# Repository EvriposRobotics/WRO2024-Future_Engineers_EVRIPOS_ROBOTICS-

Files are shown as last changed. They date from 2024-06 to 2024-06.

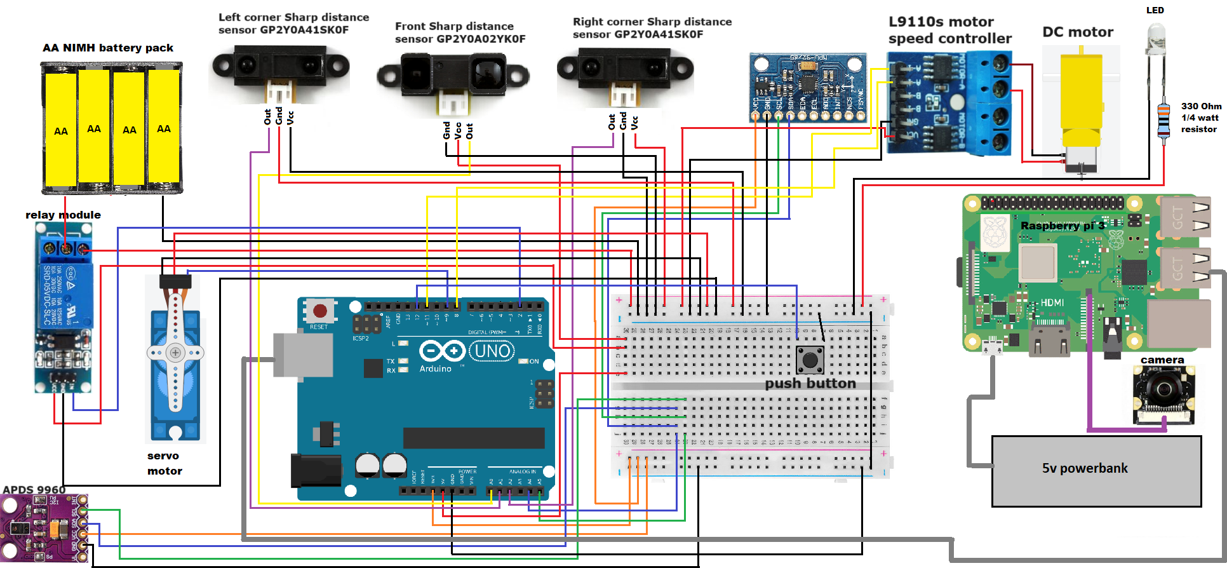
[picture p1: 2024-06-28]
schemes/electronics_wiring.png

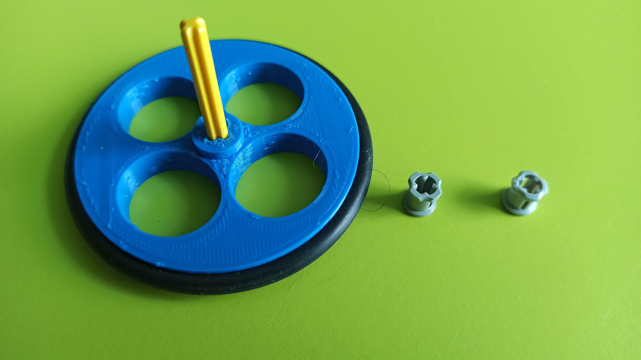
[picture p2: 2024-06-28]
models/front wheel semi-assembled.jpg

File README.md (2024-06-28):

**Evripos Robotics General Project Description (Future Engineers WRO 2023)**

The robot consists of a chassis that is entirely designed by Evripos Robotics team, excluding the rear axle mounted differential for which we used the design by "Luciano Ricardo de Faria", taken from the thingiverse.com repository :
 ([https://www.thingiverse.com/thing:3270976]).
 
The chassis was 3D printed using the "Creality Ender 3 v2" 3d printer with the use of PLA type plastic. Some sanding may need after 3D printing on some parts in order to have a perfect fit with others parts or to rotate freely depending on the case.

Not printed parts are:
- Τhe wheels axles, which are LEGO axles. On the front wheels, 2 LEGO axles with a length of 39mm have been used using a clamp (LEGO bush) on each wheel. For the    rear wheels we used 2 LEGO axles of 72mm length. A small amount of silicone-teflon type lubricating grease has been placed at each friction-contact point of the axles      with other components.
- One rubber O-ring on each wheel, outer diameter 68mm and thickness 4mm. It is critical that the o-rings are of a good quality in order to have a good grip with the    track.
   
**Robot movement**

For the drive of the robot, a "tt dc gear motor" type motor was used operating at 3-6V voltage with maximum rotation speed of 130 rpm. The motor is powered by a battery pack of 4 AA NiMH batteries connected in series.

Speed control of the robot is performed by an L9110s dc motor controller which receives signal through the digital ports 8 & 11 of the Arduino. Port 11 provides a PWM type signal for speed control. For better control of the surrounding environment through the robot's sensors, the motor speed has not been set to the motor’s maximum speed, as the PWM high-low pulse ratio does not exceed 50% (50% PWM).

The steering control is done by a micro servo type motor (MG90s) with metal gears. The Arduino controls the rotation of the servomotor via digital port 9. The servomotor rotates at most of 50⁰ left or right relative to the straight line of movement resulting to the turn of the front wheels to the relevant angle/direction.

**Robot start**

To be able to start the robot for the challenges of the competition we connected a push button switch which gives a signal to the digital port 12 of the Arduino.

**Sensors**

Three (3) distance sensors, a color sensor, an accelerometer-gyroscope(IMU) and a wide camera are used for the needs of the robot's navigation inside the track:

- The front distance sensor: "Sharp GP2Y0A02YK0F" type infrared distance sensor with 4.5-5.5V power supply tolerance and 20-150cm distance detection range.
- The left and right corner distance sensors: "Sharp GP2Y0A41SK0F" type infrared distance sensors with 4.5-5.5V power supply tolerance and 4-30cm distance detection range.
- The color sensor: "APDS9960" type sensor with voltage supply of 3.3V which communicates with the Arduino using the I2C protocol. The sensor is powered from the Arduino Uno 3.3v power supply.
- Accelerometer-gyroscope sensor: “MPU6500” IMU type sensor with 3V-5V operating voltage which communicates with the Arduino using the I2C protocol. The sensor is powered from the Arduino Uno 3.3v power supply.
- Camera: “Waveshare Raspberry Pi camera module fisheye lens(m)” camera type sensor with 5MP resolution and 200° viewing angle.

(The two sensors that communicate using the I2C protocol are connected to the Arduino through the analog input ports A4 & A5 which have the role of the SDA and SCL ports of the protocol respectively).

**In details**

The front distance sensor (GP2Y0A02YK0F) is used to detect the walls of the track ahead, while the corner ones (GP2Y0A41SK0F) are used to detect if the vehicle approaches laterally to a wall or an obstacle.

When the robot gets close to a wall then the Arduino compares the 2 inputs it receives from the 2 corner distance sensors (left/right), compares the two distance inputs and then turns towards the direction of the sensor providing the higher distance (left/right).

Through the built-in motion processor (DMP-Digital Motion Processor) contained in the “MPU6500” sensor, which combines data from the accelerometer and the gyroscope, we continuously identify the orientation of the robot (in degrees) versus its initial position on the track. The sensor orientation error is less than 1⁰. When initializing the vehicle, the sensor initilization process sets the orientation to 0⁰. When the vehicle turns left the degrees increase up to 179.9⁰. When the robot turns right the degrees are reduced up to -179.9°. Out vehicle makes use o an algorithm which constantly corrects the path of the robot according to the continuously calculated desired path. 

The color sensor “APDS9960” detects the blue and orange lines of the track in order to accurately measure the number of turns the robot has performed but also to detect the direction to which the robot should turn to. If, for example, the robot meets the blue line first, then it understands that it should follow a counterclockwise trajectory on the track and thus must turn left on every at each subsequent corner.

The detection of the green & red pillars on the track is done through the raspberry pi model b+ which receives images through a 200⁰ fisheye camera with 5MP. At first the image is cropped, discarding the upper part of it as this is not needed for the obstacle detection and could create deviations if it detects off-track objects (keep only the useful track related image). In like manner, the left and right edges of the image is cropped reducing by a small degree the viewing angle of 200o that is not needed in our case, because the fisheye lens makes a black area nearly the edges of the received image.The raspberry pi processes the images by first cropping part of the field of view and then applying (via the opencv computer vision library) an algorithm that recognizes the red and green signals (obstacles) on the track. We apply a thershold above which a red or a green pillar is detected. Without the threshold the algorithm makes faulty detections of red or color objects. The we apply an algorithm that keeps only the largest colored object it detects. This object is that we must pass from left or right side accordingly to its color. The size of the object is calculated from its detected height.The walls of the track, which are black in color, are also detected for the robot in order to avoid them. The color system used to identify colors is HSV (Hue-Saturation-Value).

Finally, these data are processed appropriately and through the serial port (USB cable) connecting the raspberry pi to the Arduino, the data are sent in the form of string messages to the Arduino. The Arduino decodes these messages and then turns accordingly to avoid obstacles, taking also into account the inputs from the other sensors it manages. One message for example is “ns” which means no obstacle is detected ahead and another message is “l12s” which means turn the wheels to the left by 12⁰. So "l" means left steering, "r" means right steering, "n" means no steering and "s" is the stop character that arduino recognizes in order to decode the received characters string.

When there are no obstacles, the Arduino moves considering only the data from the other sensors (except the camera). 

**Light source & color detection**

We use a "cool white" color Light Emmitting Diode (LED), mounted at the bottom of the robot, next to the APDS9960 sensor. The purpose of this LED is to provide a strong light for the color sensor to make precise measurements of the track bottom colors. The led is connected to the power source using a 330 Ohm 1/4 Watt resistor in series as a protection. When the white color intensity falls bellow a level it means that the vehicle passing over a colored line. Then we check the dominant color. The color model of this sensor is RGB (Red-Green-Blue). So if the vehicle passing over a blue line the dominant color is blue and if passing over an orange line the dominant color is red.

**Electric power sources**

Two power sources are used:
1. A battery pack of 4 AA NiMH batteries in series (capacity 2450mAh) producing a total output voltage of 4.8V and is used for:
- the dc motor controller which powers the robot dc motor 
- the servo motor that helps the robot turn right or left
- the front infrared distance sensor
- the two (2) corner infrared distance sensors
- the white led
  
For more efficient energy consumption management of the electronic components powered by the above battery array, a relay board is used. This relay receives a logic level (5V) activation signal from the digital output port 2 of the Arduino Uno as soon as it starts, thus powering all connected devices to the battery pack. When the robot completes the activity on the track, the Arduino Uno is turning off by the user disconnecting its power cable, so that the relay stops powering these devices.

(**Caution:** Alkaline batteries should not be used for the array as the total voltage they produce (6V) is greater than the maximum allowable operating voltage of some electrical elements powered by the battery array).

2. A Χiaomi Powerbank (Mi powerbank 3 – 22.5W) with a total capacity of 10000mAh which exclusively powers the raspberry pi with an operating voltage of 5V via a USB micro B type cable. 

Notes about the power supply:
- The camera connected to the raspberry pi is powered through the CSI type cable connected to the corresponding port of the raspberry pi.
-	The Arduino is powered through the raspberry pi's USB port via a Male-A to Male-B USB cable.
-	The MPU6500 and APDS9960 sensors are powered by the 3.3V output of the Arduino Uno.

**SBC and SCM** 

The Single Board Computer used in our setup is the Raspberry Pi 3 model B+. The SBC in our case collects and processes the data (images) from the wide angle camera, at a rate of about 20-25 frames per second. Through this setup our robot is able to detect whether it has a red or a green pillar ahead or a black wall, deciding this way the angle the wheels must turn to avoid them the right way. The Raspberry Pi runs the official Raspberry Pi OS installed on a 32GB microsd card.

The Single Board Microcontroller used is the Arduino Uno rev2. The SBM receives data from various sensors and from the SBC via a serial (USB) cable. The SBM makes the final decisions for the robots movement (when to start, when to stop and when to turn) as it gives priority to the appropriate sensor according to the circumstances.

**Programming languages**

The Arduino Uno rev2  SBM used in our robot was programmed using the Arduino IDE 1.8.19 integrated programming environment with C++ language. The libraries used for Arduino are:
-	I2Cdev.h
-	MPU6050_6Axis_MotionApps20.h
-	Wire.h
-	Servo.h
-	Adafruit_APDS9960.h

Raspberry pi 3 SBC programming was done through Thonny integrated programming environment over Raspberry OS operating system. The programming language used was Python version 3.9.2, using extensively the opencv computer vision library. Other Python libraries used:
-	numpy
-	cv2 (opencv)
-	time
-	serial

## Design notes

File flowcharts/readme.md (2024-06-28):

**This folder contains the flowcharts that out algorithm follows for the WRO 2023 Future Engineer challenges:**
- The open challenge algorithm flowchart
- The obstacle challenge algorithm flowchart

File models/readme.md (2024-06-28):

**3D model of our vehicle**

For the 3D model of the robotic vehicle our team designed we provide a Tinkercad link:
https://www.tinkercad.com/things/f08WOoFHfk0?sharecode=AVScY2sZLryFHhnb4G2e9Pp45QpsDUL6hJvRQdBMmLM

We also extracted all the parts from entire model to .stl files and created a folder which contains these files that need to be 3d printed.

All the 3d design has been made using the online 3D modelling tool www.tinkercad.com.

Parts shown in black color represent the various electronic and electric devices used for the robot, so they are not need to be printed. Also the lego axles and bushes used for the wheels mounting are also shown in black color and they are not need to be printed. In green are the rubber o-rings which play the role of tires for our vehicle. These o-rings must be of 68mm outer diameter and and 4mm thickness. We chose them to be so thin so that our vehicle would have flexibility and could be easily driven with a small dc motor. 

Everything else shown in red color should be 3D printed. Parts fixation has been made using mostly m3 and some m2 bolts. The m2 bolts are used only for the parts that are mounted the upper plastic surface like the camera,the SBC and the SBM fixation, the prototype board etc. These board have small holes and m3 bolts cannot fin. Some parts do not need bolts to fit together as they designed for press fitting (for example, the wheels with the lego axles).

We include two photos showing the assembly of the front wheels. We use a lego technic yellow axle of 5L length and two grey lego technic bush bushings for each wheel. Lego bushings are used to secure the wheel on the 3d printed wheel hub.

We used the Ultimaker Cure 5.1.0 tool as a slicer. We used a Creality Ender 3 V2 3d printer to 3d print the parts. PLA plastic seems to be sturdy enough for the needs of the WRO Future Engineer contest and we have no accidents of broken parts so far.

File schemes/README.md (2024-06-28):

**Electronic/electric components wiring diagram**
The color of the cable indicates the type of function/connection it performs:

**Caution!!!
For the electronic components of the vehicle to work properly, the ground of the nimh battery pack (4x AA) must be connected to one of the ground points (marked as GND) on the arduino board.**

For easier management and connection of the power supply lines of the electronic components we have created a prototype board on which we have soldered a line for the 5v power supplies (from the nimh batteries) and a line for the grounding. Also on the same board we have placed a switch which serves to start the robot. The one pin of the button is connected to the ground and the other to the digital port 12 of arduino, used as a input for this case. The same thing can be done using a breadboard.

We included a 5v relay board to the output of which we have connected the 5v power supply from the battery. The relay is normally open and when it is given a high signal command from digital output 2 of the arduino then the circuit is closed and the electronic components that require 5v voltage are powered. In this way we save significant amounts of energy from the nimh battery pack and our vehicle gets much more autonomy.
The only devices powered by 3.3v are the mpu6050 gyroscope and the apds-9960 color sensor.

 - Wires in gray color: the two USB cables that connect a)Arduino Uno with Raspberry Pi 3 (usb type B cable) and b)Raspberry Pi 3 with the powerbank (usb micro B cable)
 - Wires in purple color: the special caCSI type cable than connects Raspberry Pi 3 to the Raspberry Pi  camera module
 - Wires in red color: the power lines at 5v.
 - Wires in orange color: the power lines at 3.3v
 - Wires in black color: the ground lines
 - Wires in the other colors: various signal input-output cables connecting on Arduino Uno

The "datasheets" subfolder inludes the datasheets of the Sharp distance sensors. The datasheets are useful because the output voltage of these sensor do not have a linear response accordingly to the calculated distance.

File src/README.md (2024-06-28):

**Source code files**

The folder named "arduino_code" contains two files:
- The one with the name "arduino_open_challenge.ino" contains the code that Arduino UNO SBM runs at the open challenge run.
- The other with the name "arduino_obstacle_challenge.ino" contains respectively the code that Arduino UNO SBM runs at the obstacle challenge run.

The folder named "raspberry_pi_code" contains the python code that Raspberry Pi 3 SBC runs to detect the colored pillars (obstacles).

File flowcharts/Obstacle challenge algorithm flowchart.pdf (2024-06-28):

### Obstacle Challenge flowchart

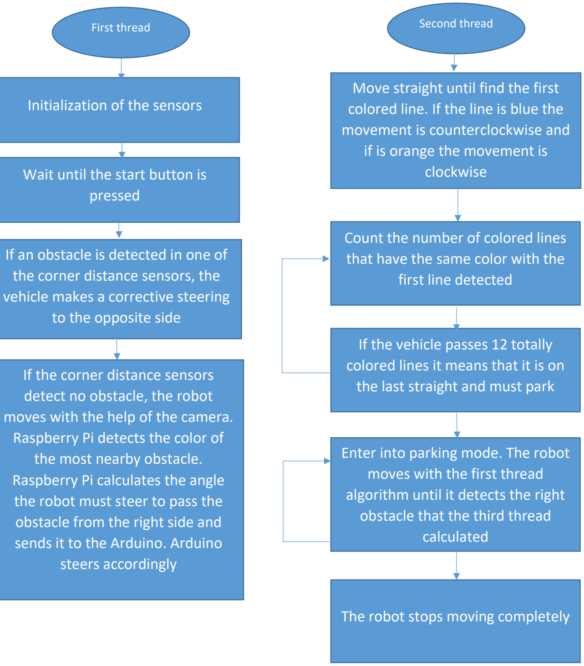
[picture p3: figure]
Initialization of the sensors; Wait until the start button is pressed; If an obstacle is detected in one of the corner distance sensors, the vehicle makes a corrective steering to the opposite side; If the corner distance sensors detect no obstacle, the robot moves with the help of the camera. Raspberry Pi detects the color of the most nearby obstacle. Raspberry Pi calculates the angle the robot must steer to pass the obstacle from the right side and sends it to the Arduino. Arduino steers accordingly; First thread; Second thread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
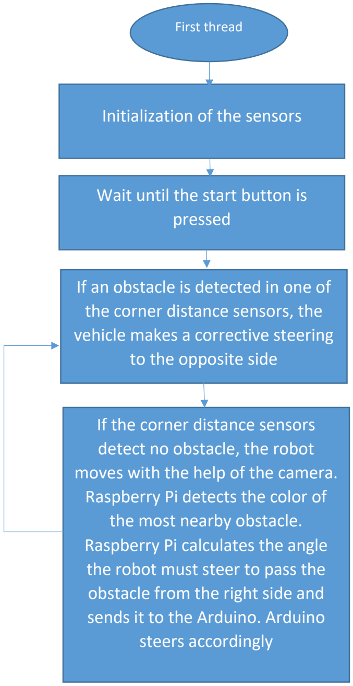
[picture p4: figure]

### Obstacle Challenge flowchart

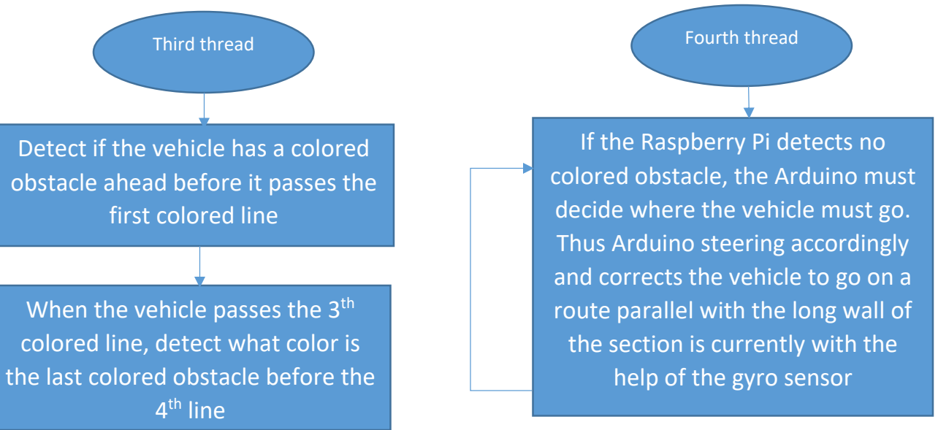
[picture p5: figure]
Detect if the vehicle has a colored obstacle ahead before it passes the first colored line; When the vehicle passes the 3; th colored line, detect what color is the last colored obstacle before the 4; th line; Third thread; Fourth thread; If the Raspberry Pi detects no colored obstacle, the Arduino must decide where the vehicle must go. Thus Arduino steering accordingly and corrects the vehicle to go on a route parallel with the long wall of the section is currently with the help of the gyro sensor
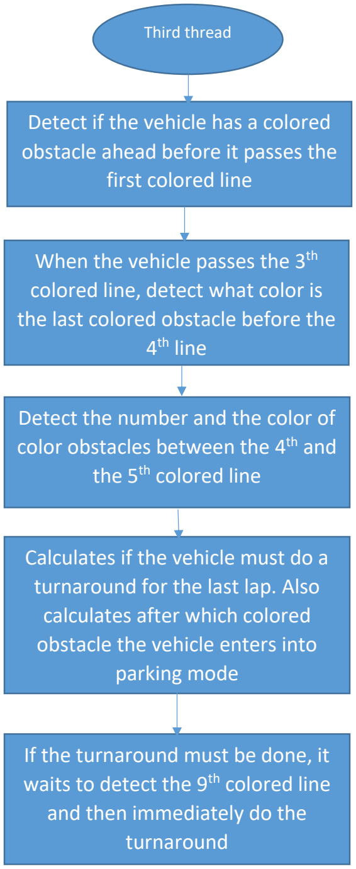
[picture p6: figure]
Detect the number and the color of color obstacles between the 4; th and; the 5; th colored line; Calculates if the vehicle must do a turnaround for the last lap. Also calculates after which colored obstacle the vehicle enters into parking mode; If the turnaround must be done, it waits to detect the 9th colored line and then immediately do the turnaround

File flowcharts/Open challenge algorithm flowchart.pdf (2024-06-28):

### Open Challenge flowchart

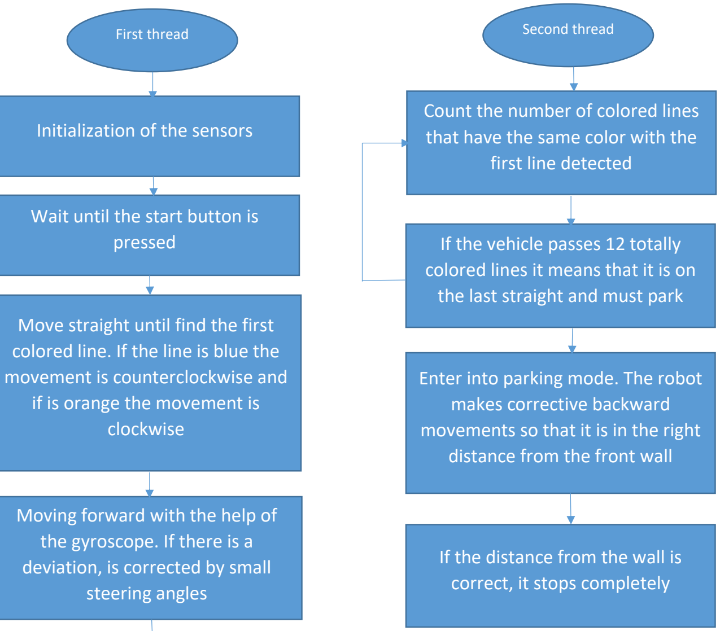
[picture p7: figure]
Initialization of the sensors; Wait until the start button is pressed; Move straight until find the first colored line. If the line is blue the movement is counterclockwise and if is orange the movement is clockwise; Moving forward with the help of the gyroscope. If there is a deviation, is corrected by small steering angles; First thread; Second thread; Count the number of colored lines that have the same color with the first line detected; If the vehicle passes 12 totally colored lines it means that it is on the last straight and must park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
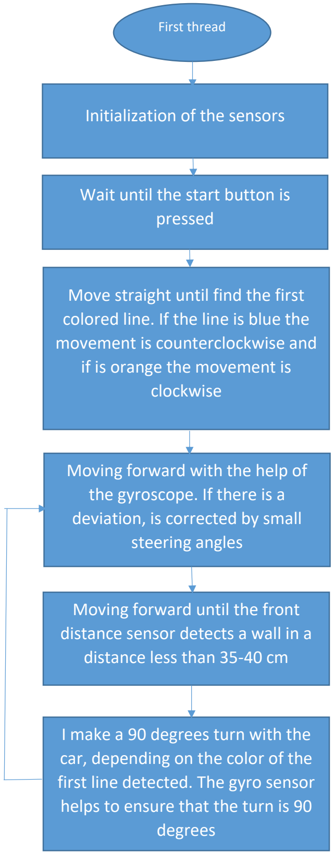
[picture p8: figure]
Moving forward until the front distance sensor detects a wall in a distance less than 35-40 cm; I make a 90 degrees turn with the car, depending on the color of the first line detected. The gyro sensor helps to ensure that the turn is 90 degrees

### Open Challenge flowchart

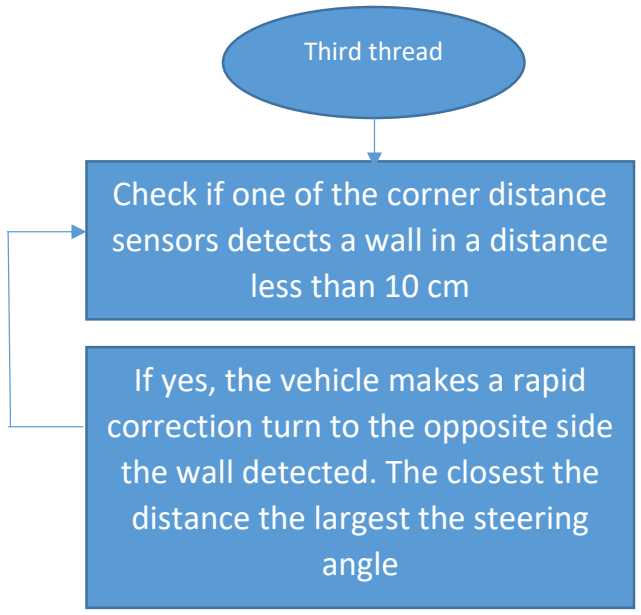
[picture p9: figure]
Check if one of the corner distance sensors detects a wall in a distance less than 10 cm; If yes, the vehicle makes a rapid correction turn to the opposite side the wall detected. The closest the distance the largest the steering angle; Third thread

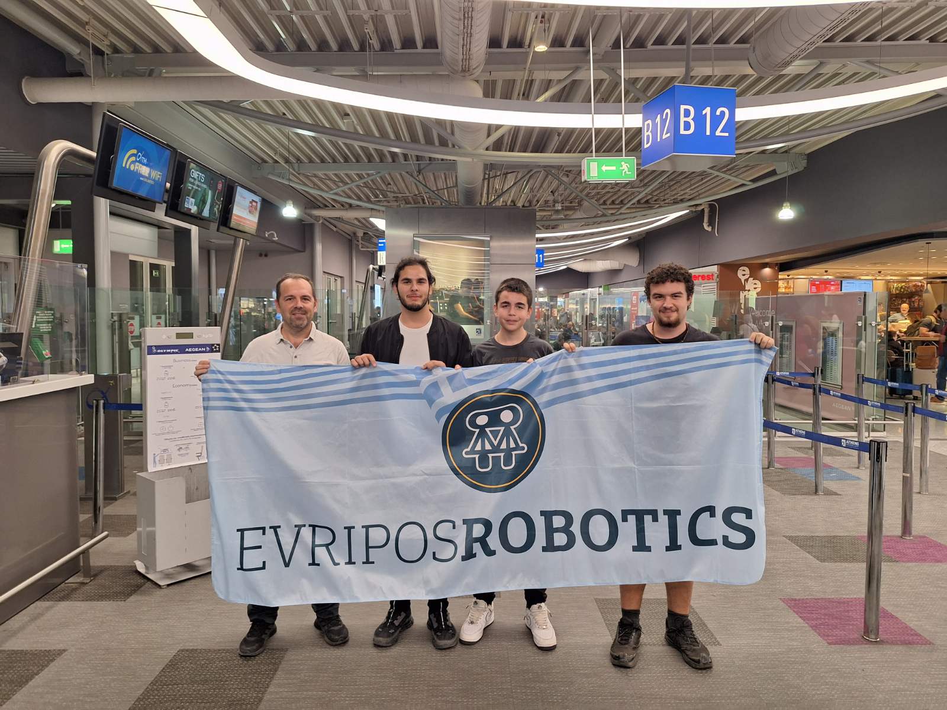
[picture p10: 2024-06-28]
t-photos/Evripos_Robotics_official_team_photo.jpg

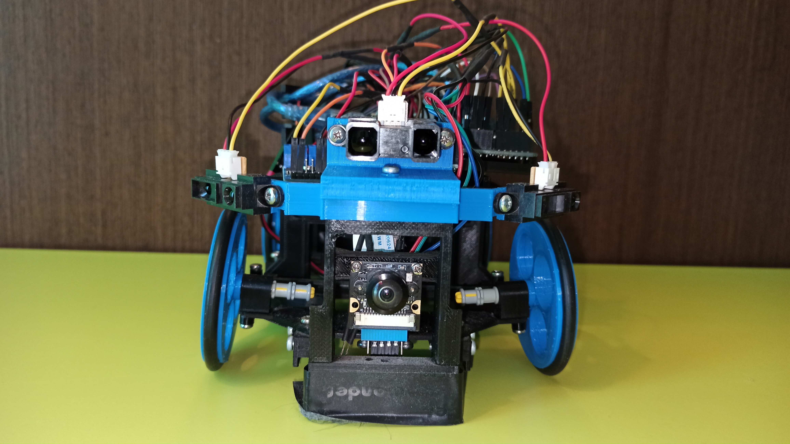
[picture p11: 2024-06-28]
v-photos/vehicle_front_side_photo.jpg

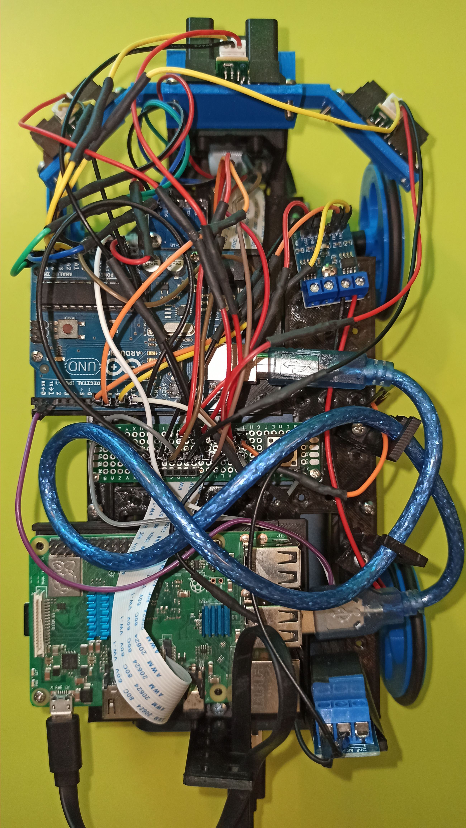
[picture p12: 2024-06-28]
v-photos/vehicle_top_side_photo.jpg

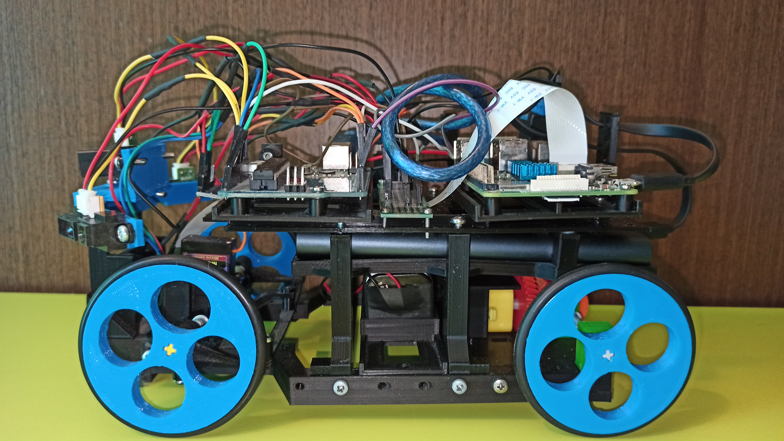
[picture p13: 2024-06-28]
v-photos/vehicle_left_side_photo.jpg

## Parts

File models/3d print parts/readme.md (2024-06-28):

This folder contains all the parts that need to be 3d printed to build the vehicle.

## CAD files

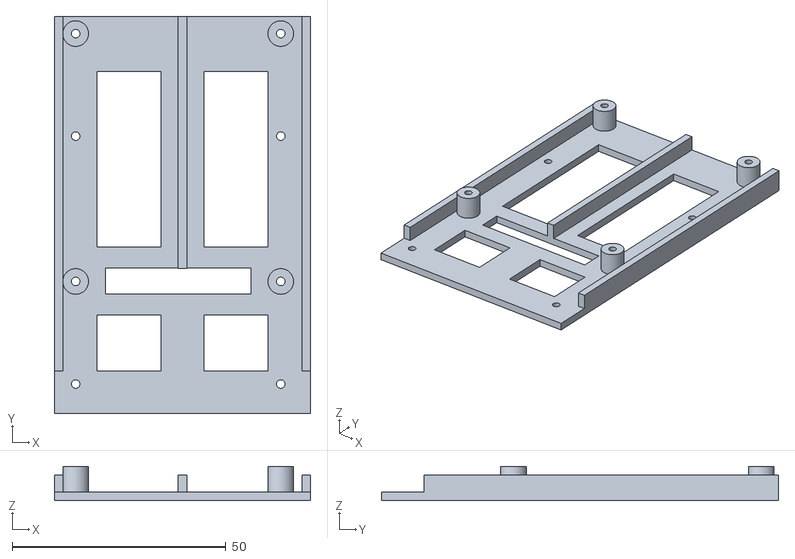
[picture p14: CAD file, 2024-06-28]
models/3d print parts/raspberry pi adapter.stl
60.0 x 92.9 x 8.00

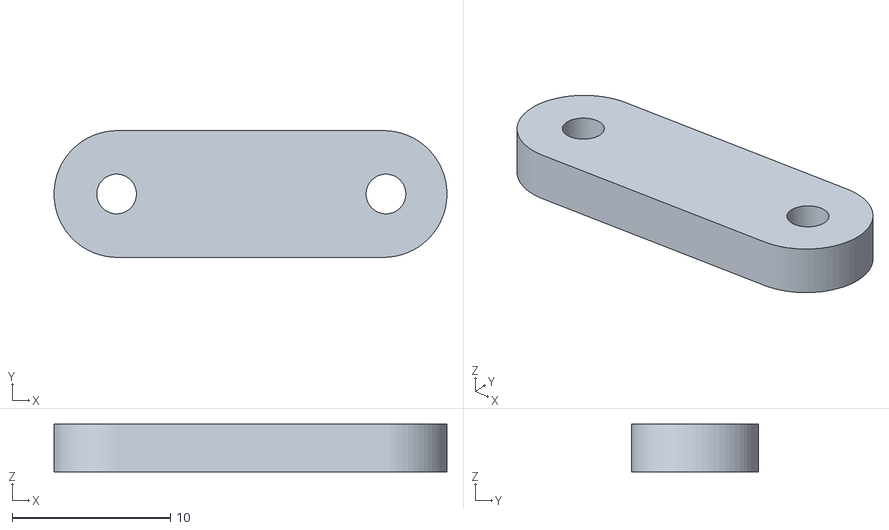
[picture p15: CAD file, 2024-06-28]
models/3d print parts/power connections hub right side adapter.stl
24.8 x 8.00 x 3.00

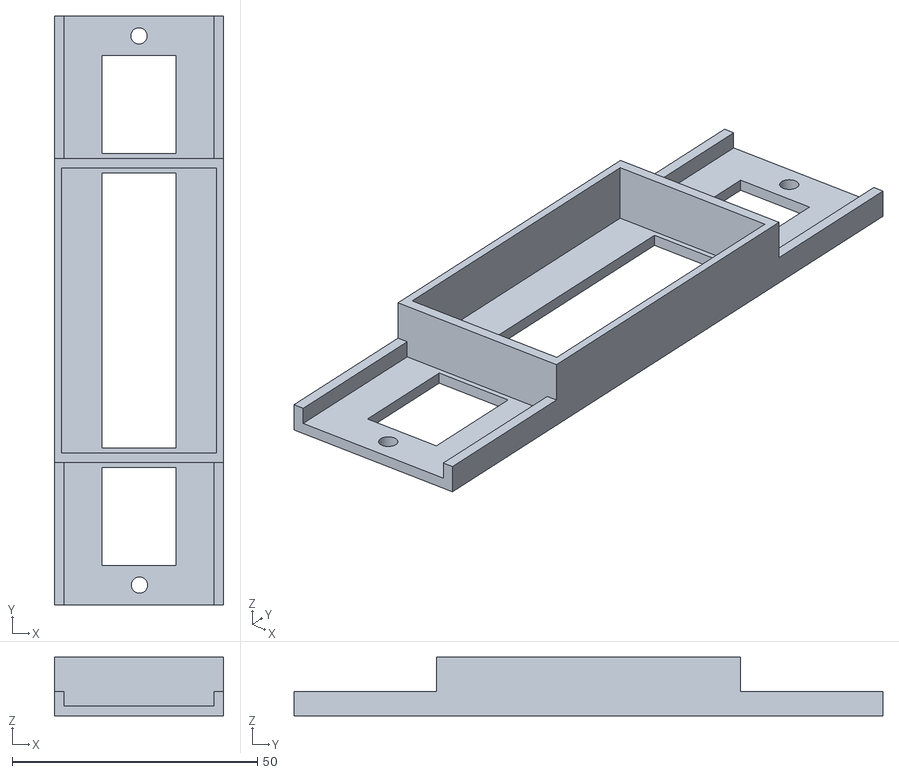
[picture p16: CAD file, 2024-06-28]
models/3d print parts/nimh battery pack case.stl
34.5 x 120.0 x 12.0

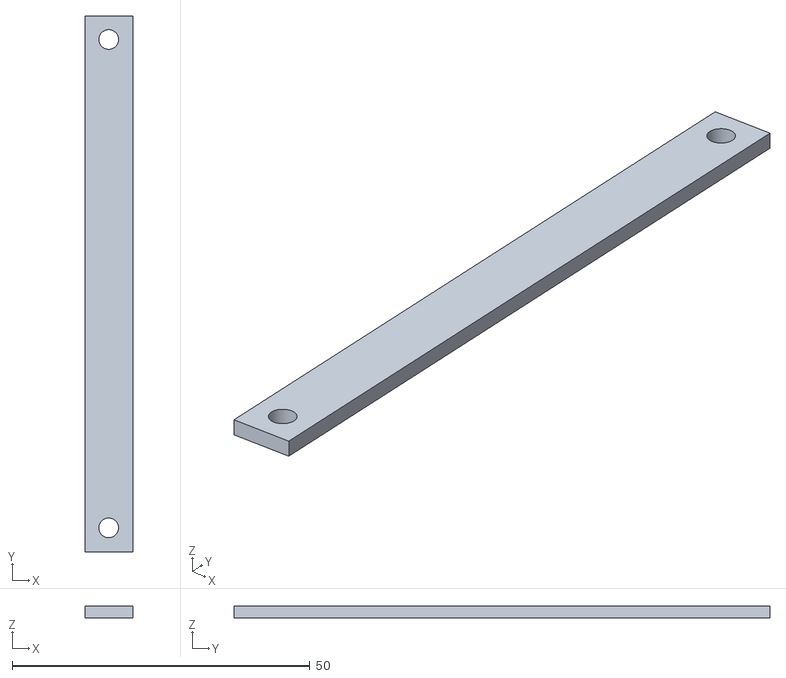
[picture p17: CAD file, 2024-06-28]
models/3d print parts/powerbank secure bar.stl
8.00 x 90.0 x 2.00

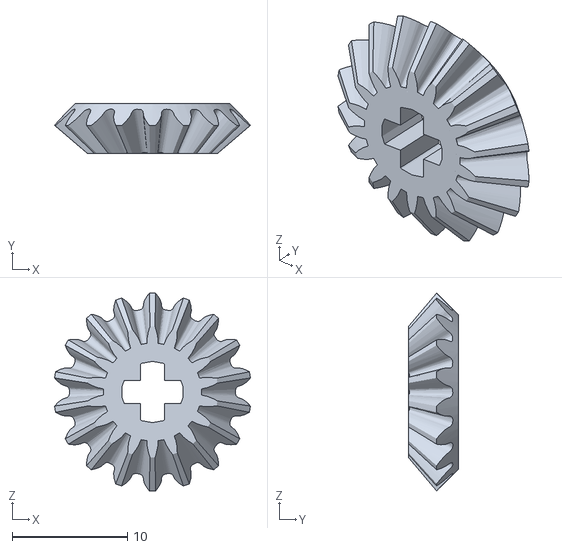
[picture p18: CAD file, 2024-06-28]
models/3d print parts/differential sun gear(print 2x times).stl
17.0 x 4.35 x 17.2

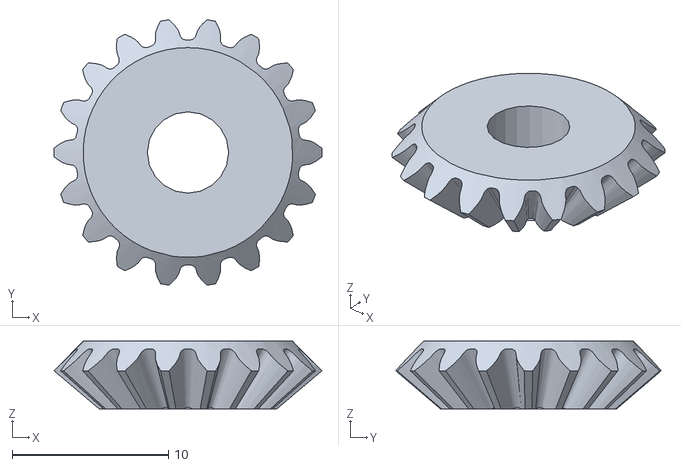
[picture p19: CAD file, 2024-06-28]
models/3d print parts/differential planet gears(print 2x times).stl
17.2 x 17.0 x 4.35

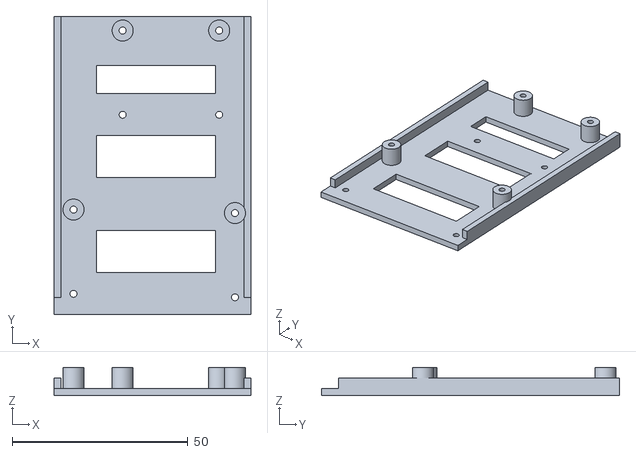
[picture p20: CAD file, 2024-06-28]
models/3d print parts/arduino adapter.stl
56.0 x 84.9 x 8.00

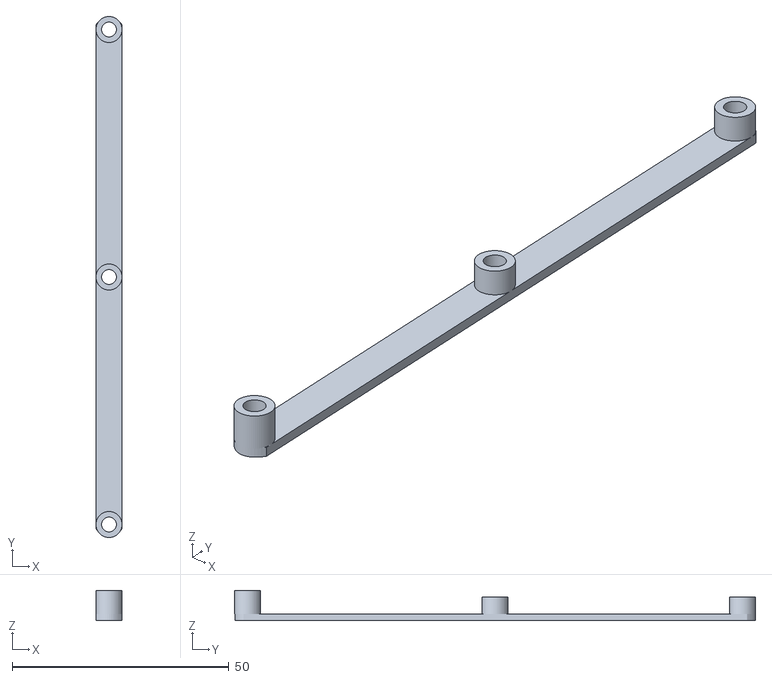
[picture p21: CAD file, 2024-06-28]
models/3d print parts/steering bar.stl
6.00 x 120.1 x 7.00

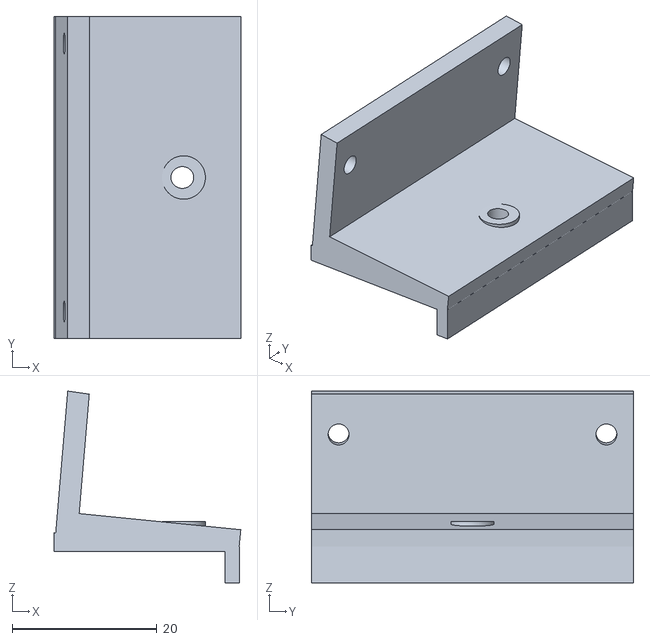
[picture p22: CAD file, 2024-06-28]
models/3d print parts/front side distance sensor mount adapter.stl
25.8 x 44.5 x 26.5

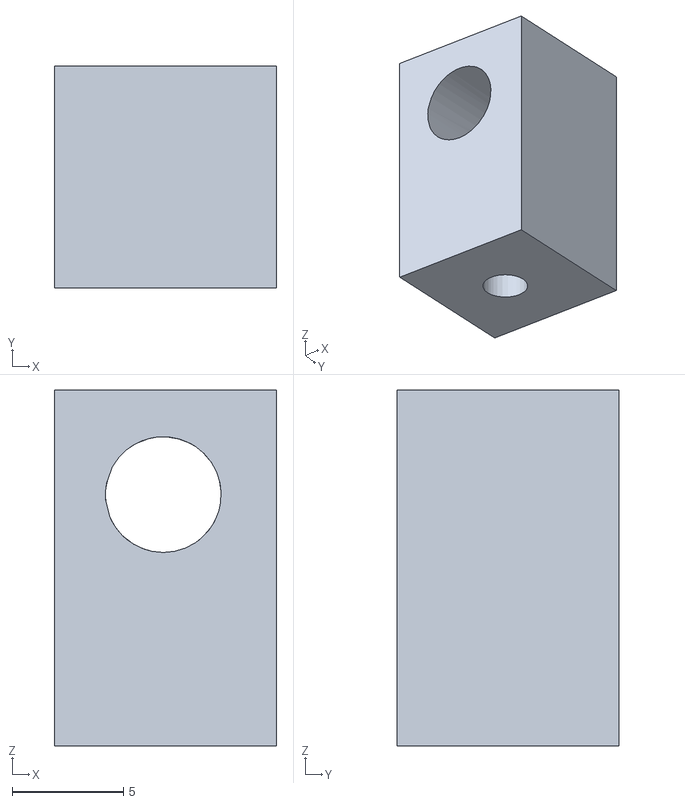
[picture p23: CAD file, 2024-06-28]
models/3d print parts/left rear axle mount(next to differntial) .stl
10.0 x 10.0 x 16.0

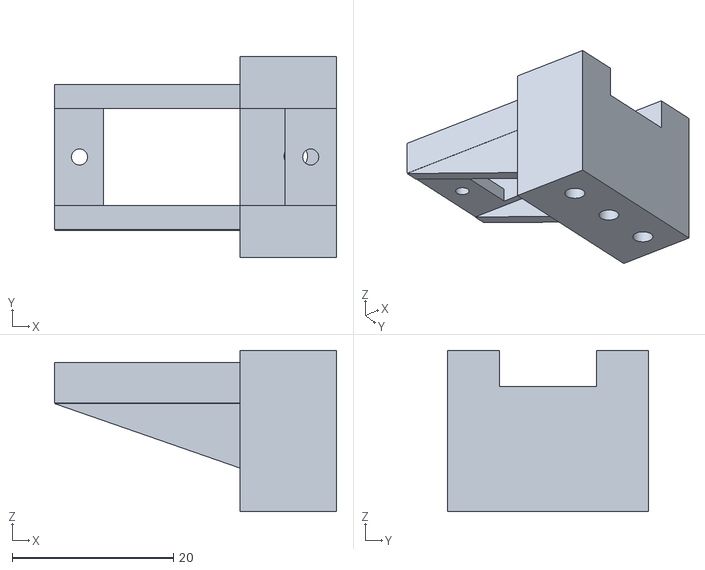
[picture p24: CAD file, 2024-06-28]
models/3d print parts/servo motor mount adapter.stl
35.0 x 25.0 x 20.0

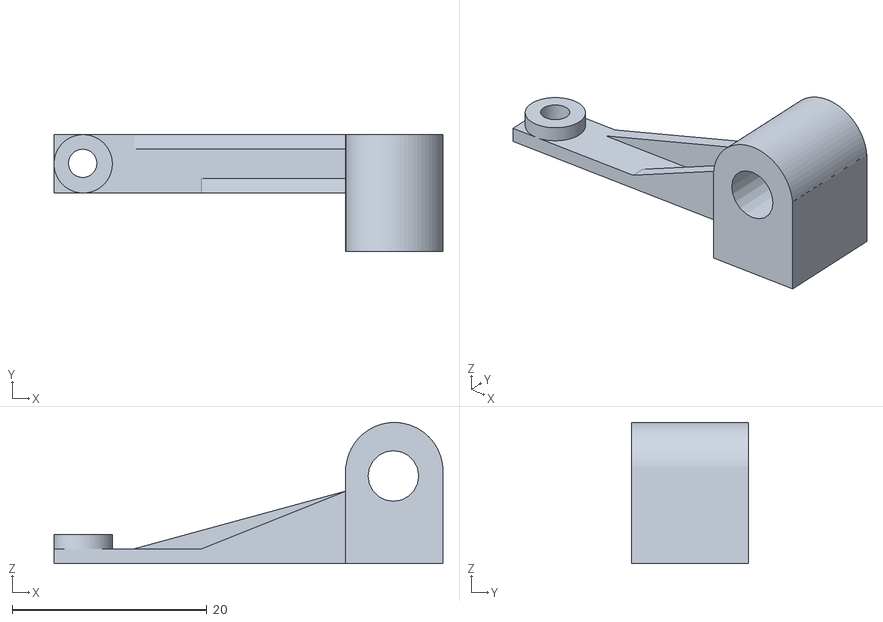
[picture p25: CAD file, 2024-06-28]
models/3d print parts/left front wheel hub.stl
40.0 x 12.0 x 14.5

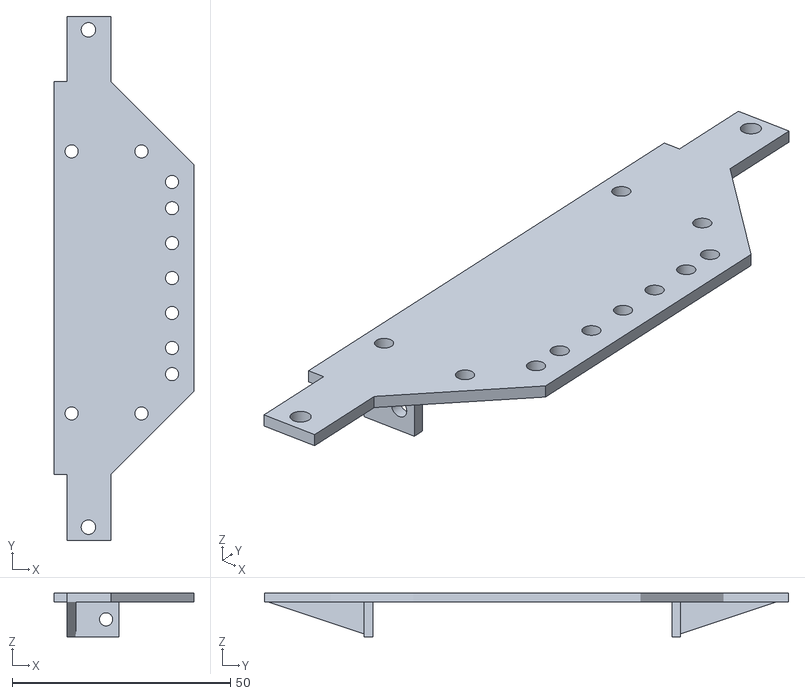
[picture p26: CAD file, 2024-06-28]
models/3d print parts/front wheels and steering servo motor adaptor.stl
32.0 x 120.0 x 10.0

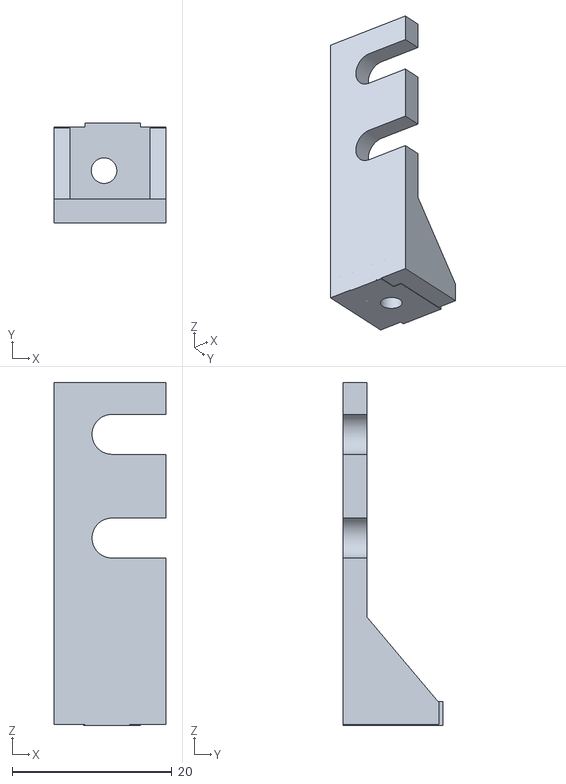
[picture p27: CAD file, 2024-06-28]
models/3d print parts/cable managmenet pillar(print 3x times).stl
14.0 x 12.5 x 43.0

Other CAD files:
models/3d print parts/right rear axle mount(next to differntial) .stl
models/3d print parts/color sensor shading attachment.stl
models/3d print parts/right rear axle mount(next to wheel) .stl
models/3d print parts/servo motor steering bar.stl
models/3d print parts/camera mount adapter.stl
models/3d print parts/corner distance sensors mount adapter.stl
models/3d print parts/dc motor and differential mount bottom plate.stl
models/3d print parts/dc motor mount plate.stl
models/3d print parts/differential case.stl
models/3d print parts/front side frame.stl
models/3d print parts/left rear axle mount(next to wheel) .stl
models/3d print parts/lower frame.stl
models/3d print parts/middle pillar(print 2x times).stl
models/3d print parts/motor ouuput gear.stl
models/3d print parts/powerbank case.stl
models/3d print parts/raspberry pi cable managmenet pillar.stl
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

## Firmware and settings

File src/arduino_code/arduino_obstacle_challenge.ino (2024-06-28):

#include "I2Cdev.h"
#include "MPU6050_6Axis_MotionApps20.h"
#if I2CDEV_IMPLEMENTATION == I2CDEV_ARDUINO_WIRE
#include "Wire.h"
#endif
MPU6050 mpu;
#include <Servo.h>
Servo myservo;
#include "Adafruit_APDS9960.h"
Adafruit_APDS9960 apds;
#define srvPin 9
#define btnPin 12
#define mPin1 8
#define mPin2 11
#define white_color 28

#define INTERRUPT_PIN 2
bool dmpReady = false;  // set true if DMP init was successful
uint8_t mpuIntStatus;   // holds actual interrupt status byte from MPU
uint8_t devStatus;      // return status after each device operation (0 = success, !0 = error)
uint16_t packetSize;    // expected DMP packet size (default is 42 bytes)
uint16_t fifoCount;     // count of all bytes currently in FIFO
uint8_t fifoBuffer[64]; // FIFO storage buffer

// orientation/motion vars
Quaternion q;           // [w, x, y, z]         quaternion container
VectorFloat gravity;    // [x, y, z]            gravity vector
float ypr[3];           // [yaw, pitch, roll]   yaw/pitch/roll container and gravity vector

volatile bool mpuInterrupt = false;     // indicates whether MPU interrupt pin has gone high
void dmpDataReady() {
  mpuInterrupt = true;
}

String fir_obs = "";
String sec_obs = "";
String th_obs = "";
String start_obs = "";
long uturn_prev;
String prev_big = "";
int uturn = 0, uturn_ok = 0;
int turnn = 0;
int must_do_uturn = 0;
int disLf, disRt;
int s = 0;
long prev = 5000;
int first_line = 1;
String first_color = "";
String color = "white";
String rec = "";
int ang, direction_angle, angle_distance ;
int in = 0; // stores incoming data from serial port
int dir = 0;
long ultraprev = 0;
long duration = 0;
long a0;
int cen = 101;
int rot = 45;
int hsp = 170, lsp = 130;
long color_delay;
int turnDir;
long stop_prev = 0;
int stop_flag = 0;
int ultra_delay = 15;
uint16_t r, g, b, c;
int d[8], maxd;
int mmax = 3;
long second_color = 0;
bool stop_first = false;
float nang = 0, add_angle = 0, diff;
int trnm;
bool obstacle;
long next_big_obstacle;
int reverse_uturn = 0;
int stop_mode = 0;

void setup() {
  Serial.begin(115200);
  pinMode(btnPin, INPUT_PULLUP);
  pinMode(13, OUTPUT);
  digitalWrite(13, HIGH);

  if (!apds.begin())
  {
    Serial.println("failed to initialize device! Please check your wiring.");
  }
  else Serial.println("Device initialized!");
  apds.enableColor(true);

  myservo.attach(srvPin);

#if I2CDEV_IMPLEMENTATION == I2CDEV_ARDUINO_WIRE
  Wire.begin();
  Wire.setClock(400000); // 400kHz I2C clock. Comment this line if having compilation difficulties
#elif I2CDEV_IMPLEMENTATION == I2CDEV_BUILTIN_FASTWIRE
  Fastwire::setup(400, true);
#endif

  Serial.println(F("Initializing I2C devices..."));
  mpu.initialize();
  pinMode(INTERRUPT_PIN, INPUT);
  Serial.println(F("Testing device connections..."));
  Serial.println(mpu.testConnection() ? F("MPU6050 connection successful") : F("MPU6050 connection failed"));

  Serial.println(F("Initializing DMP..."));
  devStatus = mpu.dmpInitialize();

  Serial.println(devStatus);



  if (devStatus == 0) {
    mpu.CalibrateAccel(6);
    mpu.CalibrateGyro(6);
    mpu.PrintActiveOffsets();
    // turn on the DMP, now that it's ready
    Serial.println(F("Enabling DMP..."));
    mpu.setDMPEnabled(true);

    // enable Arduino interrupt detection
    Serial.print(F("Enabling interrupt detection (Arduino external interrupt "));
    Serial.print(digitalPinToInterrupt(INTERRUPT_PIN));
    Serial.println(F(")..."));
    attachInterrupt(digitalPinToInterrupt(INTERRUPT_PIN), dmpDataReady, RISING);
    mpuIntStatus = mpu.getIntStatus();

    // set our DMP Ready flag so the main loop() function knows it's okay to use it
    Serial.println(F("DMP ready! Waiting for first interrupt..."));
    dmpReady = true;

    // get expected DMP packet size for later comparison
    packetSize = mpu.dmpGetFIFOPacketSize();
  }
  else
  {
    Serial.print(devStatus);
    Serial.println(F(")"));
  }




  pinMode(mPin1, OUTPUT);
  pinMode(mPin2, OUTPUT);


  myservo.write(cen);
  digitalWrite(13, LOW);

  while (digitalRead(btnPin) == HIGH)
  {
    delay(10);
  }

  pinMode(2, OUTPUT);
  digitalWrite(2, HIGH);
  analogWrite(mPin2, 0);

  /*for (int i = 0; i < 8; i++)
    {
    d[i] = 100;
    }*/
}


//================ LOOP =========================
void loop() {

  //read accelerometer sensor
  if (mpu.dmpGetCurrentFIFOPacket(fifoBuffer)) { // Read from the gyroscope/accelerometer sensor
    mpu.dmpGetQuaternion(&q, fifoBuffer);
    mpu.dmpGetYawPitchRoll(ypr, &q, &gravity);
    direction_angle = ypr[0] * 180 / M_PI;
    //Serial.print("(arduino) angle= "); Serial.println(direction_angle);
    //    Serial.print("ypr\t");
    //    Serial.println(ang);
  }  


  //read bottom color sensor
  if (apds.colorDataReady())
  {
    apds.getColorData(&r, &g, &b, &c);
    if (c < white_color && millis() - color_delay > 500)
    {

      if (r > g && r > b && first_line == 1)
      {
        prev = millis();

        trnm = turnn % 4;
        add_angle = add_angle + 1;
        if (trnm == 0) nang = -90;
        else if (trnm == 1) nang = 180 + add_angle;
        else if (trnm == 2) nang = 90 + add_angle;
        else if (trnm == 3) nang = add_angle;

        s++;
        turnn++;

        Serial.print("(arduino) s= "); Serial.println(s);
        Serial.print("(arduino) first_color= "); Serial.println("orange");
        Serial.print("(arduino) nang= "); Serial.println(nang);
        first_color = "orange";
        color = "orange";
        first_line = 0;
      }
      else if (b > g && b > r && first_line == 1)
      {
        prev = millis();

        trnm = turnn % 4;
        if (trnm == 0) nang = 90 + add_angle;
        else if (trnm == 1) nang = 180 + add_angle;
        else if (trnm == 2) nang = -90 + add_angle;
        else if (trnm == 3) nang = add_angle;

        s++;
        turnn++;

        Serial.print("(arduino) s= "); Serial.println(s);
        Serial.print("(arduino) first_color= "); Serial.println("blue");
        Serial.print("(arduino) nang= "); Serial.println(nang);
        first_color = "blue";
        color = "blue";
        first_line = 0;
      }
      else if (r > g && r > b && millis() - prev > 4000 && first_line == 0 && first_color == "orange")
      {
        trnm = turnn % 4;
        add_angle = add_angle + 1;
        if (trnm == 0) nang = -90;
        else if (trnm == 1) nang = 180 + add_angle;
        else if (trnm == 2) nang = 90 + add_angle;
        else if (trnm == 3) nang = add_angle;

        s++;
        if (s == 8)
          fir_obs = prev_big;
        if (s == 12)
          prev_big = "";
        turnn++;

        Serial.print("(arduino) s= "); Serial.println(s);
        Serial.print("(arduino) nang= "); Serial.println(nang);

        if (s == 8 || s == 4)
        {
          duration += millis() - prev;
        }
        prev = millis();
        color = "orange";
      }
      else if (b > g && b > r && millis() - prev > 4000 && first_line == 0 && first_color == "blue")
      {


        trnm = turnn % 4;
        if (trnm == 0) nang = 90 + add_angle;
        else if (trnm == 1) nang = 180 + add_angle;
        else if (trnm == 2) nang = -90 + add_angle;
        else if (trnm == 3) nang = add_angle;

        s++;
        if (s == 8)
          fir_obs = prev_big;
        if (s == 12)
          prev_big = "";
        turnn++;

        Serial.print("(arduino) s= "); Serial.println(s);
        Serial.print("(arduino) nang= "); Serial.println(nang);

        if (s == 8 || s == 4)
        {
          duration += millis() - prev;
        }
        prev = millis();
        color = "blue";
      }
      else
      {
        color = "white";
      }
    }
  }

  if (trnm == 1) //convert negative angle to a positive one
  {
    if (direction_angle <= -135)
      direction_angle = direction_angle + 360;
  }


  //============= uturn code ===============
  if ( s == 9 && uturn == 0 && uturn_ok == 0)
  {
    uturn_ok = 1;
    Serial.print(fir_obs); Serial.print("-"); Serial.print(sec_obs); Serial.print("-");
    Serial.print(th_obs); Serial.print("-"); Serial.print(start_obs); Serial.println("");
    if (fir_obs != "" && sec_obs != "" && th_obs != "")
    {
      if (sec_obs == "RED")
      {
        must_do_uturn = 1;

      }
    }
    else if (th_obs == "")
      if (start_obs != "" && fir_obs == "RED")
      {
        must_do_uturn = 1;

      }
    if (start_obs == "" && sec_obs == "RED")
    {
      must_do_uturn = 1;

    }

    if (must_do_uturn == 1)
    {
      Serial.println("must_do_uturn");
      if (th_obs == "GREEN" || (th_obs == "" && start_obs == "GREEN"))
        reverse_uturn = 1;
      turnn -= 2;
      uturn = 1;
      if (s == 9)
        s = 8;
    
      if (th_obs == "GREEN")
        myservo.write(cen + 40);
      else
        myservo.write(cen - 40); 
      analogWrite(mPin2, hsp);
      
      if (first_color == "orange")
        first_color = "blue";
      else if (first_color == "blue")
        first_color = "orange";
    }
  }

  if (uturn == 1 && reverse_uturn == 0 && abs(direction_angle - 90) < 10)
  {
    uturn = 0;
    
    myservo.write(cen);
    digitalWrite(mPin1, HIGH);
    digitalWrite(mPin2, HIGH);
    uturn = 2;
    myservo.write(cen + 35);
    uturn_prev = millis();
    
    analogWrite(mPin2, 0);
    analogWrite(mPin1, lsp);
  }
  else if (uturn == 1 && reverse_uturn == 1 && abs(-90 - direction_angle) < 10)
  {
    uturn = 0;
    
    myservo.write(cen);
    digitalWrite(mPin1, HIGH);
    digitalWrite(mPin2, HIGH);
    uturn = 2;
    myservo.write(cen - 35); 
    uturn_prev = millis();
    
    analogWrite(mPin2, 0);
    analogWrite(mPin1, lsp);
  }



  if (uturn == 2 && reverse_uturn == 0 && dir == 0)
  {
    analogWrite(mPin2, 0);
    analogWrite(mPin1, lsp);
  }
  else if (uturn == 2 && dir != 0 && reverse_uturn == 0 &&  millis() - uturn_prev > 500)
  {
    uturn = 0;
    analogWrite(mPin1, 0);
    analogWrite(mPin2, hsp);
    nang = 180;
  }
  else if (uturn == 2 && reverse_uturn == 1 &&  millis() - uturn_prev > 500 && abs(direction_angle - 180) < 10)
  {
    uturn = 0;
    analogWrite(mPin1, 0);
    analogWrite(mPin2, hsp);
    nang = 180;
  }


  if (s == 12 && stop_flag == 0)
  {
    stop_flag = 1;
    if (must_do_uturn == 0) //no uturn
      if (th_obs == "")
        if (start_obs == "")
          stop_mode = 1; //stop after 1st obstacle
        else
          stop_mode = 2; //stop after find big obstacle and do back movement
      else
        stop_mode = 1; //stop after 1st obstacle
    else //uturn done
      if (start_obs != "")
        stop_mode = 1; //stop after 1st obstacle
      else
        stop_mode = 2; //stop after find big obstacle and do back movement
  }

  if (stop_flag == 1 && prev_big != "" && stop_mode == 1)
  {
    prev = millis();
    stop_flag = 2;
  }
  else if (stop_flag == 1 && prev_big != "" && stop_mode == 2)
  {
    digitalWrite(mPin1, HIGH);
    digitalWrite(mPin2, HIGH);
    analogWrite(mPin2, 0);
    analogWrite(mPin1, lsp);
    myservo.write(cen);
    prev = millis();
    stop_flag = 3;
  }

  if (stop_flag == 2 && millis() - prev > 1500)
  {
    digitalWrite(mPin1, HIGH);
    digitalWrite(mPin2, HIGH);
    while (true)
    {
      delay(5);
    }
  }
  else if (stop_flag == 3 && millis() - prev > 1500)
  {
    digitalWrite(mPin1, HIGH);
    digitalWrite(mPin2, HIGH);
    while (true)
    {
      delay(5);
    }
  }



  if (digitalRead(btnPin) == LOW)
  {
    analogWrite(mPin2, lsp);
    color_delay = millis();
  }

  //read messages from serial
  if (Serial.available() > 0)
  {
    // read the incoming byte:
    in = Serial.read();
    if (in == 71 || in == 82)
    {
      if (in == 82)
      {
        if (s == 8 && sec_obs == "")
        {
          sec_obs = "RED";
          next_big_obstacle = millis();
        }
        if (s == 8 && sec_obs != "" && th_obs == "" && millis() - next_big_obstacle > 1000)
        {
          th_obs = "GREEN";
        }
        prev_big = "RED";
        if (s == 0)
          start_obs = "RED";
        Serial.println("RED!!!");
      }
      else
      {
        if (s == 8 && sec_obs == "")
        {
          sec_obs = "GREEN";
          next_big_obstacle = millis();
        }
        if (s == 8 && sec_obs != "" && th_obs == "" && millis() - next_big_obstacle > 1000)
        {
          th_obs = "GREEN";
        }
        prev_big = "GREEN";
        if (s == 0)
          start_obs = "GREEN";
        Serial.println("GREEN!!!");
      }
    }
    else if (in != 115)
    {
      rec = rec + (char)in;
    }
    else
    {

      if (rec[0] == char(108)) dir = -1;
      else if (rec[0] == char(114)) dir = 1;
      else if (rec[0] == char(110)) dir = 0;

      rec.remove(0, 1);
      ang = rec.toInt();

      rec = "";
    }
  }

  //read from corner distance sensors
  if (uturn == 0)
  {
    //8cm = 1.58v = 323 arduino read value
    //4cm = 2.7v = 553 arduino read value
    disLf = analogRead(A1);
    disRt = analogRead(A2);
    if (disLf > 300)
    {
      angle_distance = (disLf - 300) / 10 + 35;
      if (angle_distance > 50)
        angle_distance = 50;
      myservo.write(cen + angle_distance);
      digitalWrite(13, HIGH);
      analogWrite(mPin2, hsp);
    }
    else if (disRt > 300)
    {
      angle_distance = (disRt - 300) / 10 + 35;
      if (angle_distance > 50)
        angle_distance = 50;
      myservo.write(cen - angle_distance);
      digitalWrite(13, HIGH);
      analogWrite(mPin2, hsp);
    }
    else
    {
      digitalWrite(13, LOW);
      analogWrite(mPin2, lsp);
      if (dir == -1)
      {
        myservo.write(cen - ang);
        if (abs(ang) > 10)
          analogWrite(mPin2, hsp);
      }
      else if (dir == 1)
      {
        myservo.write(cen + ang);
        if (abs(ang) > 10)
          analogWrite(mPin2, hsp);
      }
      else if (dir == 0)
      {
        if (disLf <= 300 && disRt <= 300)
        {
          diff = abs(direction_angle - nang); 
          if (diff > 30)
            diff = 30;
          if (diff < -30)
            diff = -30;
          
          if (nang > direction_angle)
          {
            myservo.write(cen - diff);
          }
          else
          {
            myservo.write(cen + diff);
          }
        }
        
        else if (first_color == "blue")
        {
          myservo.write(cen - rot);
        }
        else if (first_color == "orange")
        {
          myservo.write(cen + rot);
        }
      }
    }
  }

}

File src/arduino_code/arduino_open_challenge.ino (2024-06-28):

#include "I2Cdev.h"
#include "MPU6050_6Axis_MotionApps20.h"
#if I2CDEV_IMPLEMENTATION == I2CDEV_ARDUINO_WIRE
#include "Wire.h"
#endif
#define INTERRUPT_PIN 2
#define meas 20
MPU6050 mpu;
#include <Servo.h>
Servo myservo;
#include "Adafruit_APDS9960.h"
Adafruit_APDS9960 apds;


long delay_prev = 0;
int mindel = 1000, maxdel = 0;

uint16_t r, g, b, c;
int s = 0;
int first_line = 1;
bool dmpReady = false;  // set true if DMP init was successful
uint8_t mpuIntStatus;   // holds actual interrupt status byte from MPU
uint8_t devStatus;      // return status after each device operation (0 = success, !0 = error)
uint16_t packetSize;    // expected DMP packet size (default is 42 bytes)
uint16_t fifoCount;     // count of all bytes currently in FIFO
uint8_t fifoBuffer[64]; // FIFO storage buffer

// orientation/motion vars
Quaternion q;           // [w, x, y, z]         quaternion container
VectorFloat gravity;    // [x, y, z]            gravity vector
float ypr[3];           // [yaw, pitch, roll]   yaw/pitch/roll container and gravity vector

volatile bool mpuInterrupt = false;     // indicates whether MPU interrupt pin has gone high
void dmpDataReady() {
  mpuInterrupt = true;
}

#define mPin1 8
#define mPin2 11
#define srvPin 9
#define btnPin 12

//long duration;
int distance;
int minDis, readA0, readA1, readA2;
int readA[25], temp;
int i, j;
int a0, a1, a2;
int disL = 45;
int parkL = 110, parkH = 160;
int cen = 96;
int rot = 35;
int rotc = 3;
int hsp = 170, lsp = 170, ssp = 255, initsp = 125; //normal hsp=130 lsp=100
int maxd;
int mmax = 3;
int disLf = 100, disRt = 100;
long dis = 500, prevdis = 500, nowdis;
long prev_wall;
//float mo;
long prev = 0;
int dir = 1;
int turn = 0;
float ang, nang, diff;
int turnn = 0, trnm;
int turnDir = 0;
int clr = 0;
long cprev, ultraprev = 0, turnprev;
int ultra_delay = 30, queue = 1;
float add_angle = 0;
int protect = 0;
long prot_pr = 0;
long sum;


void setup() {

  pinMode(btnPin, INPUT_PULLUP);
  pinMode(13, OUTPUT);
  digitalWrite(13, HIGH);

  Serial.begin(115200);

#if I2CDEV_IMPLEMENTATION == I2CDEV_ARDUINO_WIRE
  Wire.begin();
  Wire.setClock(400000); // 400kHz I2C clock. Comment this line if having compilation difficulties
#elif I2CDEV_IMPLEMENTATION == I2CDEV_BUILTIN_FASTWIRE
  Fastwire::setup(400, true);
#endif

  Serial.println(F("Initializing I2C devices..."));
  mpu.initialize();
  pinMode(INTERRUPT_PIN, INPUT);
  Serial.println(F("Testing device connections..."));
  Serial.println(mpu.testConnection() ? F("MPU6050 connection successful") : F("MPU6050 connection failed"));

  Serial.println(F("Initializing DMP..."));
  devStatus = mpu.dmpInitialize();

  Serial.println(devStatus);



  if (devStatus == 0) {
    mpu.CalibrateAccel(6);
    mpu.CalibrateGyro(6);
    mpu.PrintActiveOffsets();
    // turn on the DMP, now that it's ready
    Serial.println(F("Enabling DMP..."));
    mpu.setDMPEnabled(true);

    // enable Arduino interrupt detection
    Serial.print(F("Enabling interrupt detection (Arduino external interrupt "));
    Serial.print(digitalPinToInterrupt(INTERRUPT_PIN));
    Serial.println(F(")..."));
    attachInterrupt(digitalPinToInterrupt(INTERRUPT_PIN), dmpDataReady, RISING);
    mpuIntStatus = mpu.getIntStatus();

    // set our DMP Ready flag so the main loop() function knows it's okay to use it
    Serial.println(F("DMP ready! Waiting for first interrupt..."));
    dmpReady = true;

    // get expected DMP packet size for later comparison
    packetSize = mpu.dmpGetFIFOPacketSize();
  }
  else
  {
    Serial.print(devStatus);
    Serial.println(F(")"));
  }

  myservo.attach(srvPin);

  if (!apds.begin())
  {
    Serial.println("failed to initialize device! Please check your wiring.");
  }
  else Serial.println("Device initialized!");
  apds.enableColor(true);
  
  pinMode(mPin1, OUTPUT);
  pinMode(mPin2, OUTPUT);

  pinMode(2, OUTPUT);
  digitalWrite(2, HIGH);

  myservo.write(cen);
  digitalWrite(13, LOW);


  while (digitalRead(btnPin) == HIGH)
  {
    delay(10);
  }
  analogWrite(mPin2, hsp);
  digitalWrite(mPin1, LOW);
  delay(300);
  analogWrite(mPin2, initsp);


  nang = add_angle;
  delay_prev = millis();
  ultraprev = millis();
  turnprev = millis();
}


//================ LOOP =========================
void loop() {

  //checks for the first line color, runs only until finds the first line
  if (first_line == 1 && apds.colorDataReady())
  {
    apds.getColorData(&r, &g, &b, &c);
    if (c < 28)
    {
      if (r > g && r > b && first_line == 1)
      {
        prev = millis();
        turnDir = 2; //2=turn right
        first_line = 0;
      }
      else if (b > g && b > r && first_line == 1)
      {
        prev = millis();
        s++;
        turnDir = 1; //1=turn left
        first_line = 0;
      }
    }
  }
  

  if (mpu.dmpGetCurrentFIFOPacket(fifoBuffer)) { // Read from the gyroscope/accelerometer sensor
    mpu.dmpGetQuaternion(&q, fifoBuffer);
    mpu.dmpGetYawPitchRoll(ypr, &q, &gravity);
    ang = ypr[0] * 180 / M_PI;    
    //    Serial.println(ang);
  }

  if (millis() - ultraprev > ultra_delay)
  {
    dis = analogRead(A0);
    Serial.print(" dis= "); Serial.print(dis);
   
    disLf = analogRead(A1);
    disRt = analogRead(A2);
    ultraprev = millis();
  }
 


  if (turn == 0 && disLf > 300)
  {
    turn = 3;
    myservo.write(cen + 15);
    prev_wall = millis();
  }

  if (turn == 0  && disRt > 300)
  {
    turn = 3;
    myservo.write(cen - 15);
    prev_wall = millis();
  }

  if (turn == 3 && millis() - prev_wall > 600)
  {
    turn = 0;
    myservo.write(cen);
  }



  //turn=0 initial state(just go straight)
  //turn=1 turn on a corner state
  //turn=2 goes stright but need a small correction steering
  //turn=3 goes straight but one of the corner distance sensors detect a nearby wall. Correction steering need
  if ((turn == 0 || turn == 2) && dis > 350 && dis < 400 && millis() - turnprev > 1500)
  {
    prev = millis();
    turn = 1;
    digitalWrite(13, HIGH);

    trnm = turnn % 4;

    if (turnDir == 1) //turn left
    {
      add_angle = add_angle - 1;
      if (trnm == 0) nang = 90 + add_angle;
      else if (trnm == 1) nang = 180 + add_angle;
      else if (trnm == 2) nang = -90 + add_angle;
      else if (trnm == 3) nang = add_angle;
      myservo.write(cen - rot);
    }
    else if (turnDir == 2) //turn right
    {
      add_angle = add_angle + 1;
      if (trnm == 0) nang = -90;
      else if (trnm == 1) nang = 180 + add_angle;
      else if (trnm == 2) nang = 90 + add_angle;
      else if (trnm == 3) nang = add_angle;
      myservo.write(cen + rot);
    }

    analogWrite(mPin2, hsp);
  }

  if (trnm == 1) //convert negative angle to a positive one
  {
    if (ang <= -135)
      ang = ang + 360;
  }
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
